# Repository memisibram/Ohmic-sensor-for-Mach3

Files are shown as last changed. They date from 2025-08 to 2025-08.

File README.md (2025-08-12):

# Ohmic-sensor-for-Mach3
Touch ohmic sensor for Mach3 plasma cutters

### About the project
This project is designed for use in plasma cutters using a Mach3 control card that communicates via a USB port.

While performing a probe search with the torch, the pilot arc cable is disabled and the torch nozzle is connected to an opamp integrated circuit. Once the probe search is complete, the pilot arc cable is reconnected, allowing the ohmic sensor to be used in HF-initiated pilot arc plasma cutters.

Project video.
 - Video: [https://youtu.be/aqT4PSTSzog](https://youtu.be/aqT4PSTSzog)

### Pictures
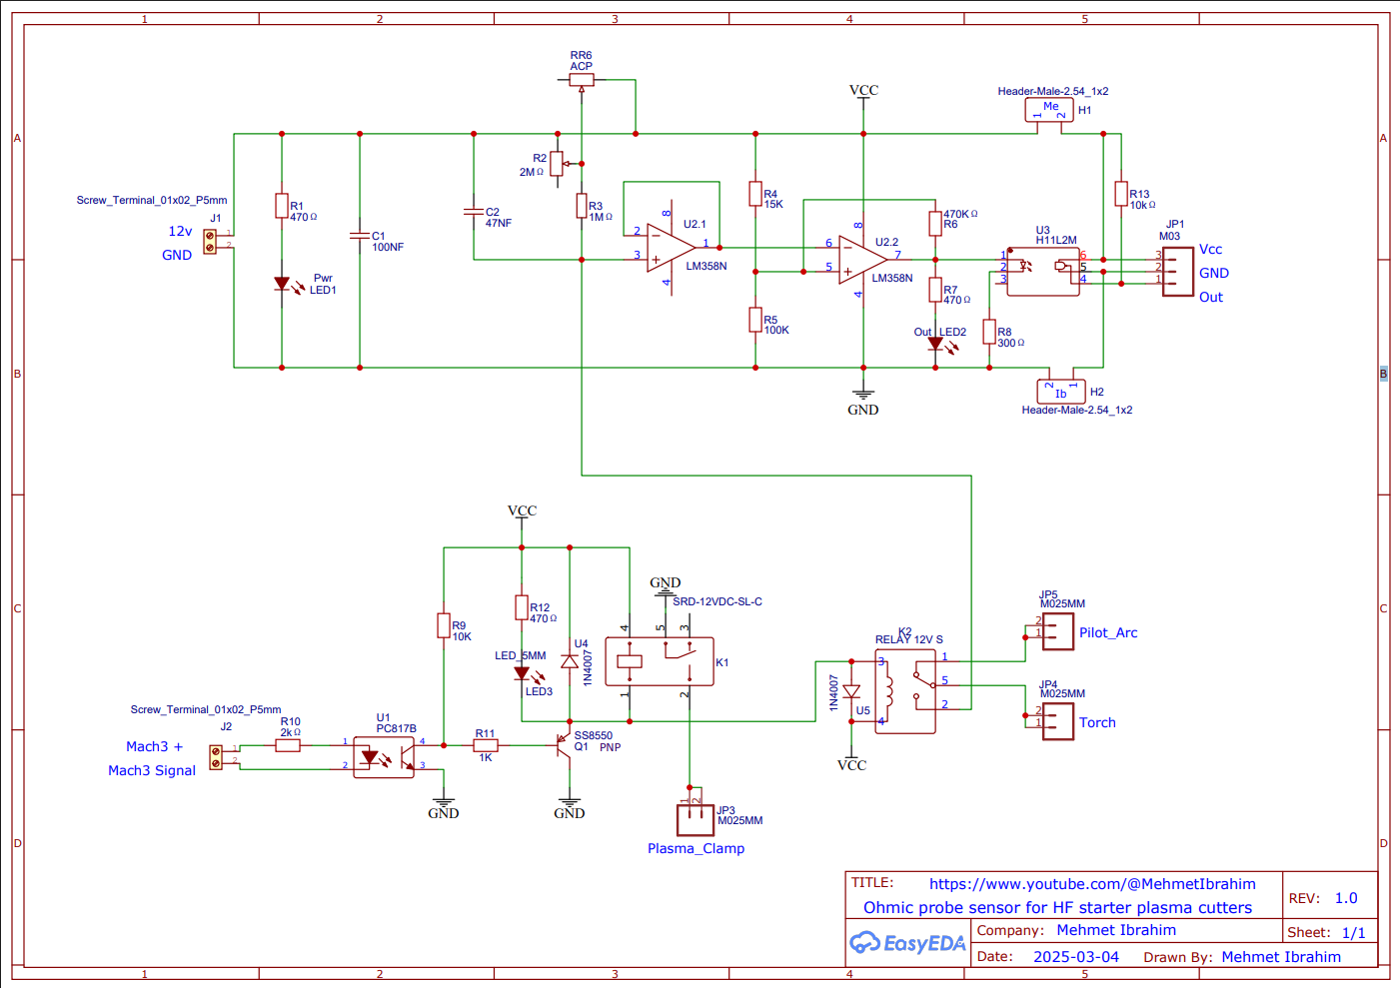
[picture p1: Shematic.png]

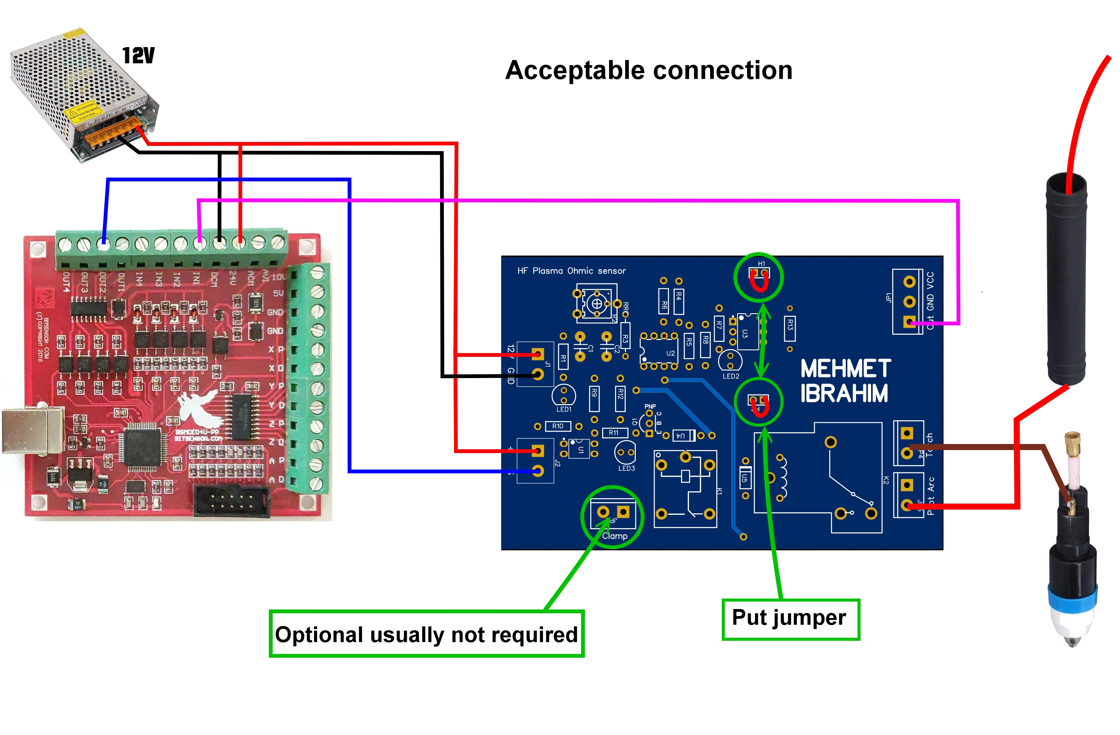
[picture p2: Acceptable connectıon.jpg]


### License GNU GPL v3.0

### Donation

  -  Paypal: memisibram@gmail.com or https://www.paypal.me/memisibram

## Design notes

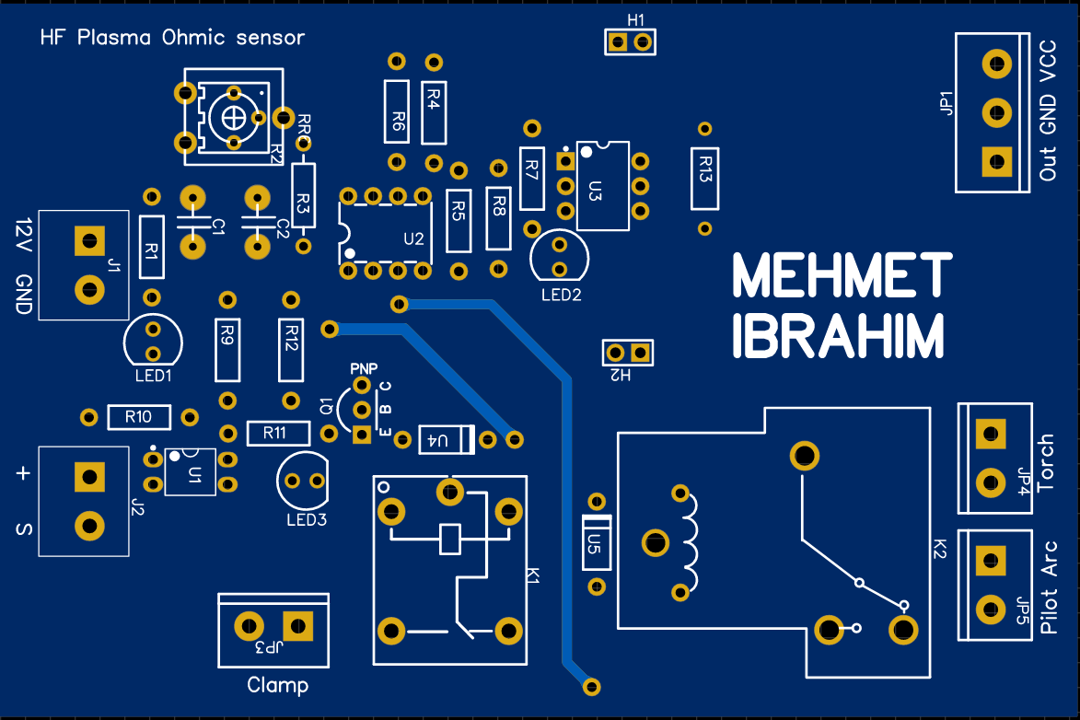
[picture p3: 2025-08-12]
Screenshot 2025-03-24 004826.png

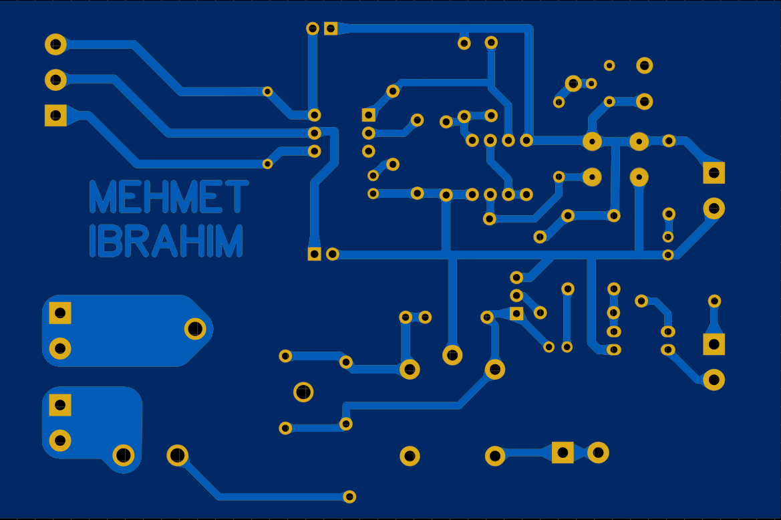
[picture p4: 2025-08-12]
Screenshot 2025-03-24 004859.png

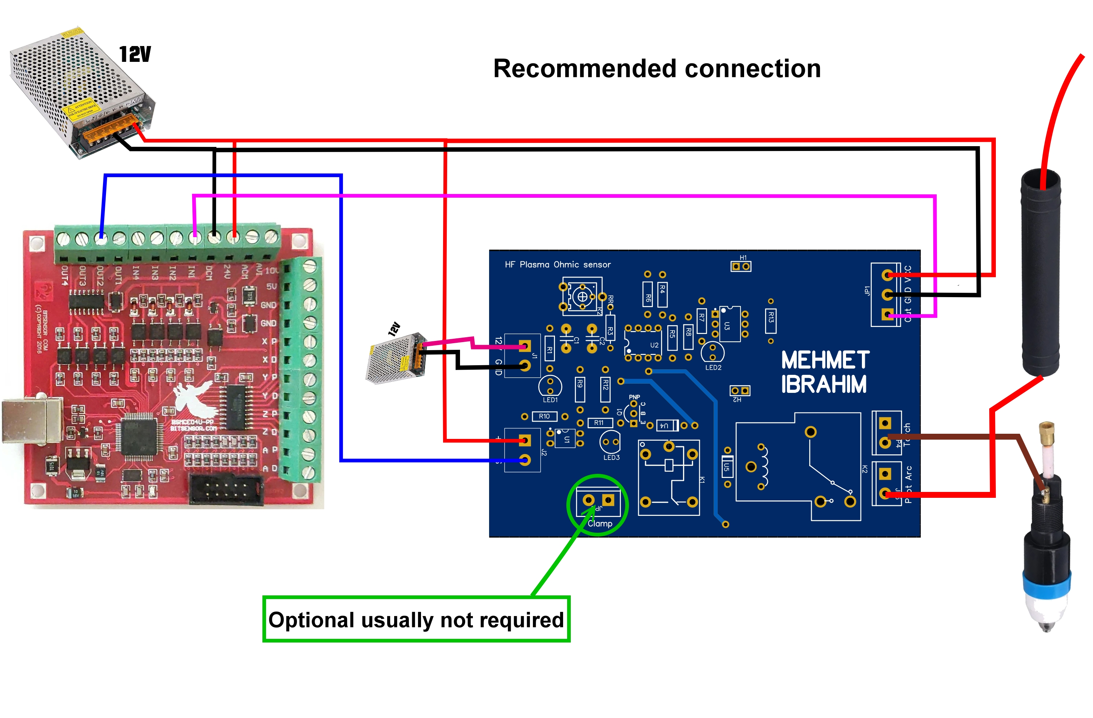
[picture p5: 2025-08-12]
Recommended connectıon.jpg

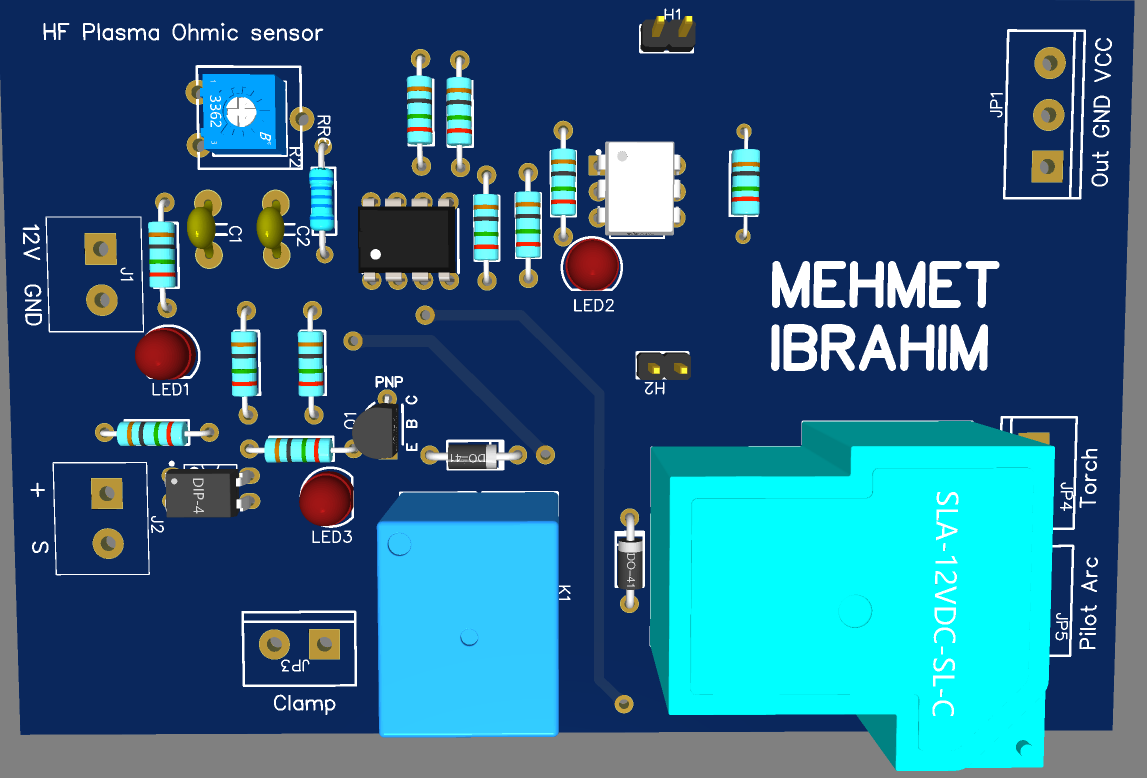
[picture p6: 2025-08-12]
Screenshot 2025-03-24 015735.png

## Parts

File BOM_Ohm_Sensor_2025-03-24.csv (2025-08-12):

ID | Name | Designator | Footprint | Quantity | Manufacturer Part | Manufacturer | Supplier | Supplier Part | Price
1 | ACP | RR6 | ACP SPAIN | 1
2 | 1MΩ | R3 | RES-TH_BD2.2-L6.5-P10.50-D0.6 | 1 | CFR0W4J0105A50 | UNI-ROYAL(厚声) | LCSC | C61306 | 0.008
3 | 2kΩ | R10 | RES-TH_BD2.4-L6.3-P10.30-D0.6 | 1 | MFR-25FRE52-2K | YAGEO(国巨) | LCSC | C1745563 | 0.011
4 | 10kΩ | R13 | RES-TH_BD2.7-L6.2-P10.20-D0.4 | 1 | CR1/4W-10K±5%-ST52 | VO(翔胜) | LCSC | C2894649 | 0.003
5 | SS8550 | Q1 | TO-92-3_L4.8-W3.7-P2.54-L | 1 | SS8550CTA | onsemi(安森美) | LCSC | C327518 | 0.107
6 | Screw_Terminal_01x02_P5mm | J2,J1 | TERMINALBLOCK_ONSHORE_1X02_P5.00MM_HORIZONTAL | 2
7 | Header-Male-2.54_1x2 | H2,H1 | HDR-TH_2P-P2.54-V-M-1 | 2 | 826629-2 | TE Connectivity(泰科电子) | LCSC | C86471 | 0.443
8 | LM358N | U2 | PDIP-8_L10.2-W5.9-P2.54-LS7.6-BL | 1 | LM358N/NOPB | TI(德州仪器) | LCSC | C83405 | 0.806
9 | 1N4007 | U5,U4 | DO-41_BD2.4-L4.7-P8.70-D0.6-RD | 2 | 1N4007 | CJ(江苏长电/长晶) | LCSC | C5261026 | 0.019
10 | H11L2M | U3 | DIP-6_L8.5-W6.4-P2.54-LS7.6-BL | 1 | H11L2M | onsemi(安森美) | LCSC | C258255 | 1.486
11 | PC817B | U1 | DIP-4_L4.6-W6.5-P2.54-LS7.6-BL | 1 | PC817B | 华润华晶 | LCSC | C115499 | 0.053
12 | 2MΩ | R2 | RES-ADJ-TH_3362P | 1 | 3362P-1-205LF | BOURNS | LCSC | C124582 | 0.342
13 | 470Ω | R12,R7,R1 | RES-TH_BD2.4-L6.3-P10.30-D0.6 | 3 | RN 1/4W 300R F T/B A1 | Tyohm(幸亚电阻) | LCSC | C410638 | 0.01
14 | 1K | R11 | RES-TH_BD2.4-L6.3-P10.30-D0.6 | 1 | RN 1/4W 300R F T/B A1 | Tyohm(幸亚电阻) | LCSC | C410638 | 0.01
15 | 10K | R9 | RES-TH_BD2.4-L6.3-P10.30-D0.6 | 1 | RN 1/4W 300R F T/B A1 | Tyohm(幸亚电阻) | LCSC | C410638 | 0.01
16 | 300Ω | R8 | RES-TH_BD2.4-L6.3-P10.30-D0.6 | 1 | RN 1/4W 300R F T/B A1 | Tyohm(幸亚电阻) | LCSC | C410638 | 0.01
17 | 470KΩ | R6 | RES-TH_BD2.4-L6.3-P10.30-D0.6 | 1 | RN 1/4W 300R F T/B A1 | Tyohm(幸亚电阻) | LCSC | C410638 | 0.01
18 | 100K | R5 | RES-TH_BD2.4-L6.3-P10.30-D0.6 | 1 | RN 1/4W 300R F T/B A1 | Tyohm(幸亚电阻) | LCSC | C410638 | 0.01
19 | 15K | R4 | RES-TH_BD2.4-L6.3-P10.30-D0.6 | 1 | RN 1/4W 300R F T/B A1 | Tyohm(幸亚电阻) | LCSC | C410638 | 0.01
20 | LED_5MM | LED3 | LED-TH_BD5.0-P2.54-FD_C9900023552 | 1 | LED_5MM | null | LCSC | C9900023552
21 | Out | LED2 | LED-TH_BD5.0-P2.54-FD_C9900023552 | 1 | LED_5MM | null | LCSC | C9900023552
22 | Pwr | LED1 | LED-TH_BD5.0-P2.54-FD_C9900023552 | 1 | LED_5MM | null | LCSC | C9900023552
23 | SRD-12VDC-SL-C | K1 | RELAY-TH_SRD-XXVDC-XL-C | 1 | SRD-12VDC-SL-C | 松乐 | LCSC | C30431 | 0.311
24 | 47NF | C2 | CERAMIC CAPACITOR 100NF | 1 | CT4-0805Y104M500 | LCSC | LCSC | undefined
25 | 100NF | C1 | CERAMIC CAPACITOR 100NF | 1 | CT4-0805Y104M500 | LCSC | LCSC | undefined
26 | M03 | JP1 | SCREWTERMINAL-5MM-3 | 1
27 | M025MM | JP5,JP4,JP3 | SCREWTERMINAL-5MM-2 | 3
28 | RELAY 12V S | K2 | RELAY-TH_SLA-12VDC-SL-C | 1 | SLA-12VDC-SL-C | SONGLE | LCSC | C125736 | 1.039

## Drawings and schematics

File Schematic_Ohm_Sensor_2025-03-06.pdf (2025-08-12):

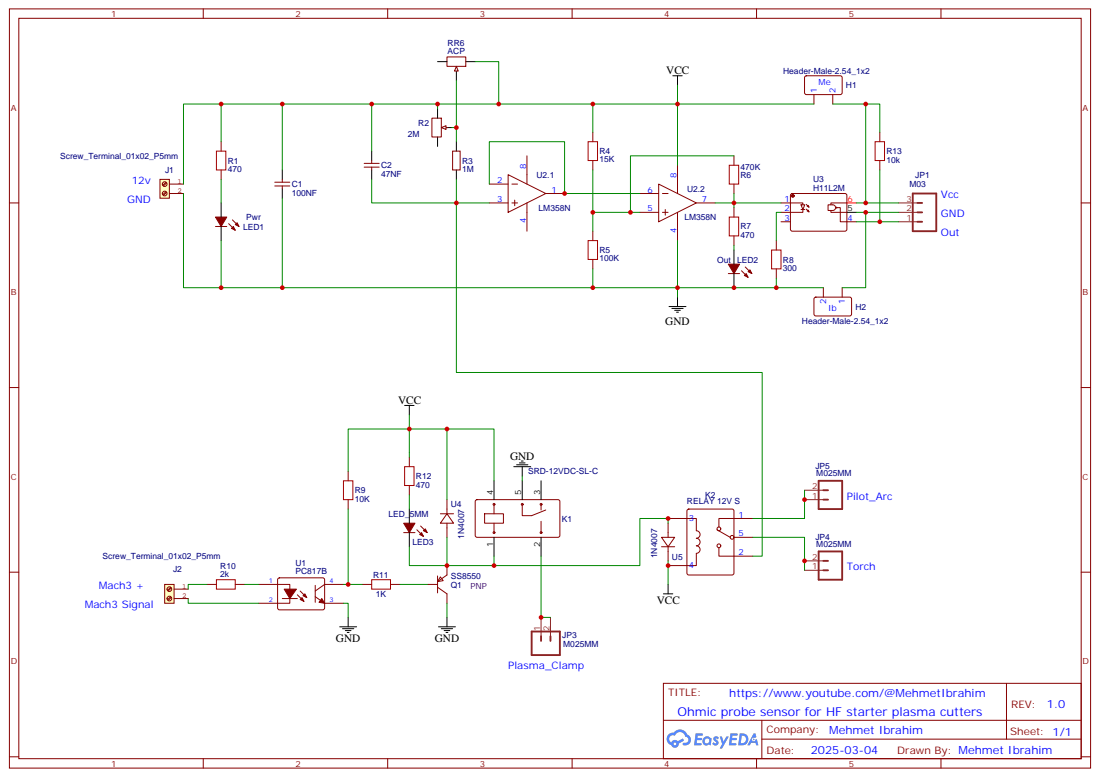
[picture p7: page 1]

TITLE:
Ohmic probe sensor for HF starter plasma cutters

https://www.youtube.com/@MehmetIbrahim

Drawn By: Mehmet Ibrahim

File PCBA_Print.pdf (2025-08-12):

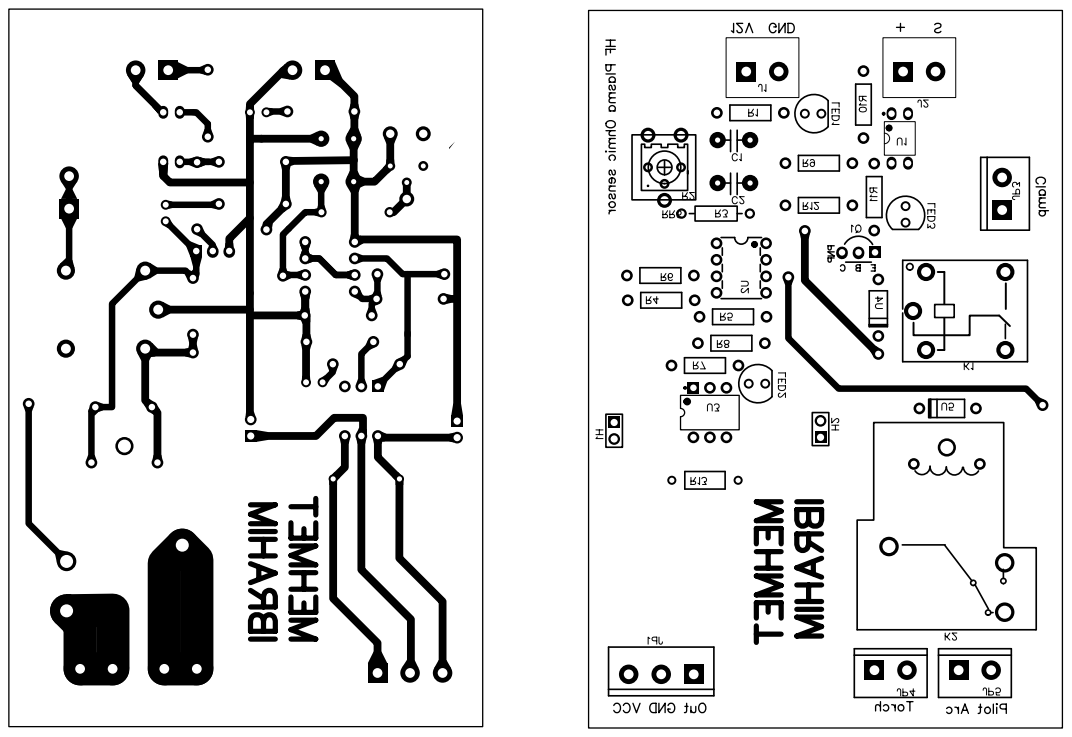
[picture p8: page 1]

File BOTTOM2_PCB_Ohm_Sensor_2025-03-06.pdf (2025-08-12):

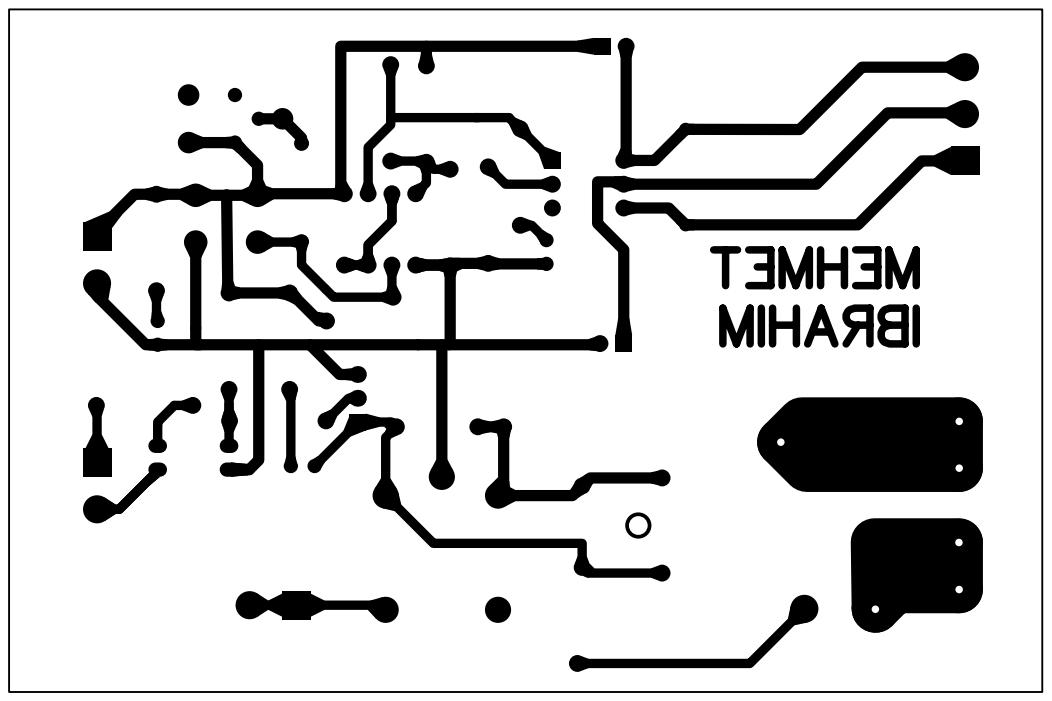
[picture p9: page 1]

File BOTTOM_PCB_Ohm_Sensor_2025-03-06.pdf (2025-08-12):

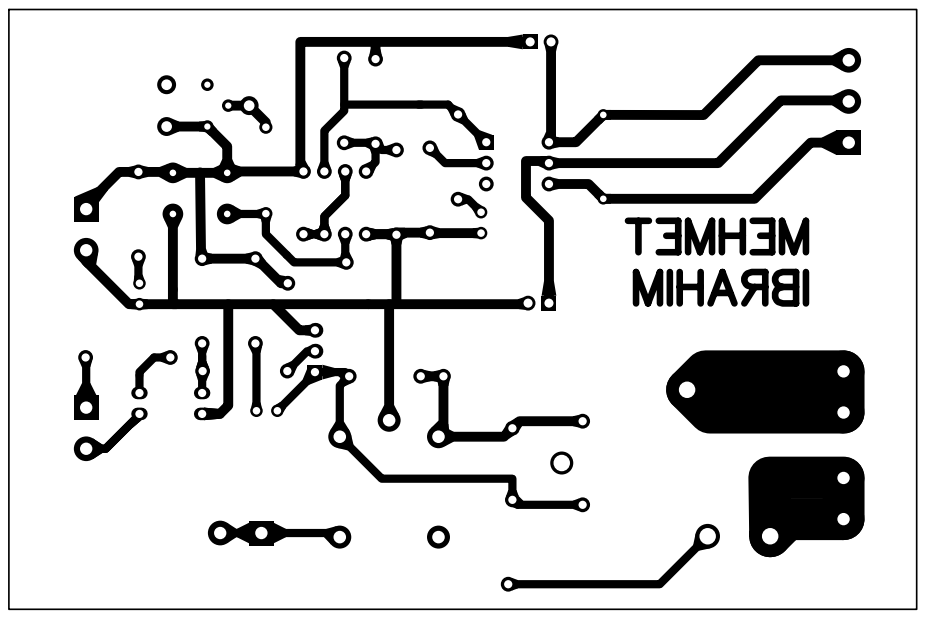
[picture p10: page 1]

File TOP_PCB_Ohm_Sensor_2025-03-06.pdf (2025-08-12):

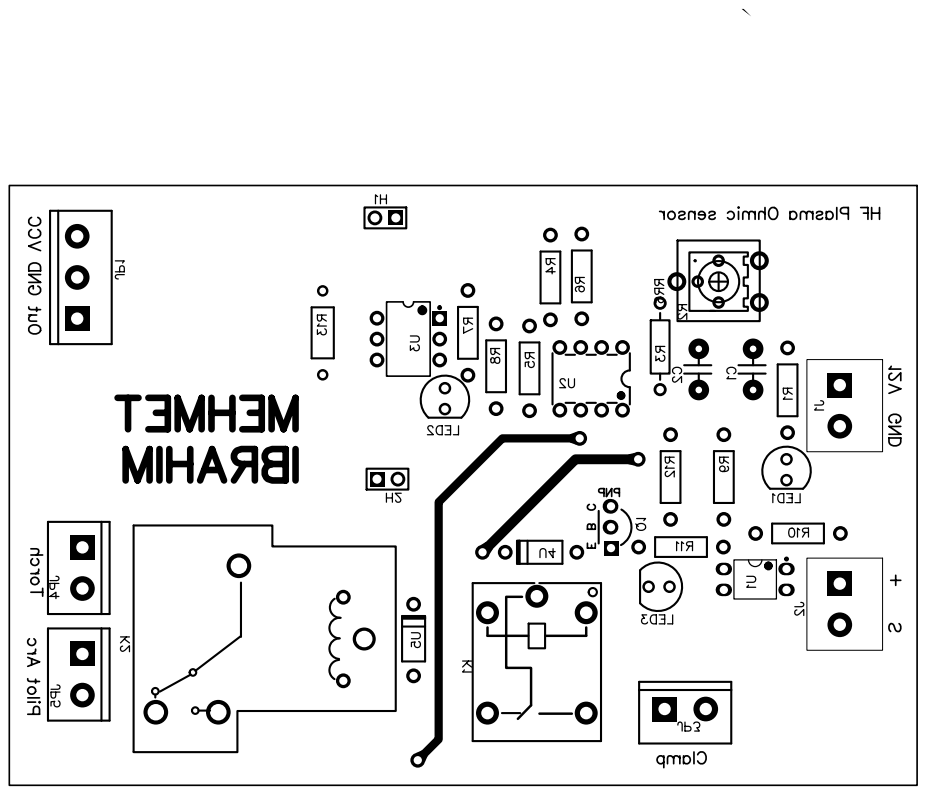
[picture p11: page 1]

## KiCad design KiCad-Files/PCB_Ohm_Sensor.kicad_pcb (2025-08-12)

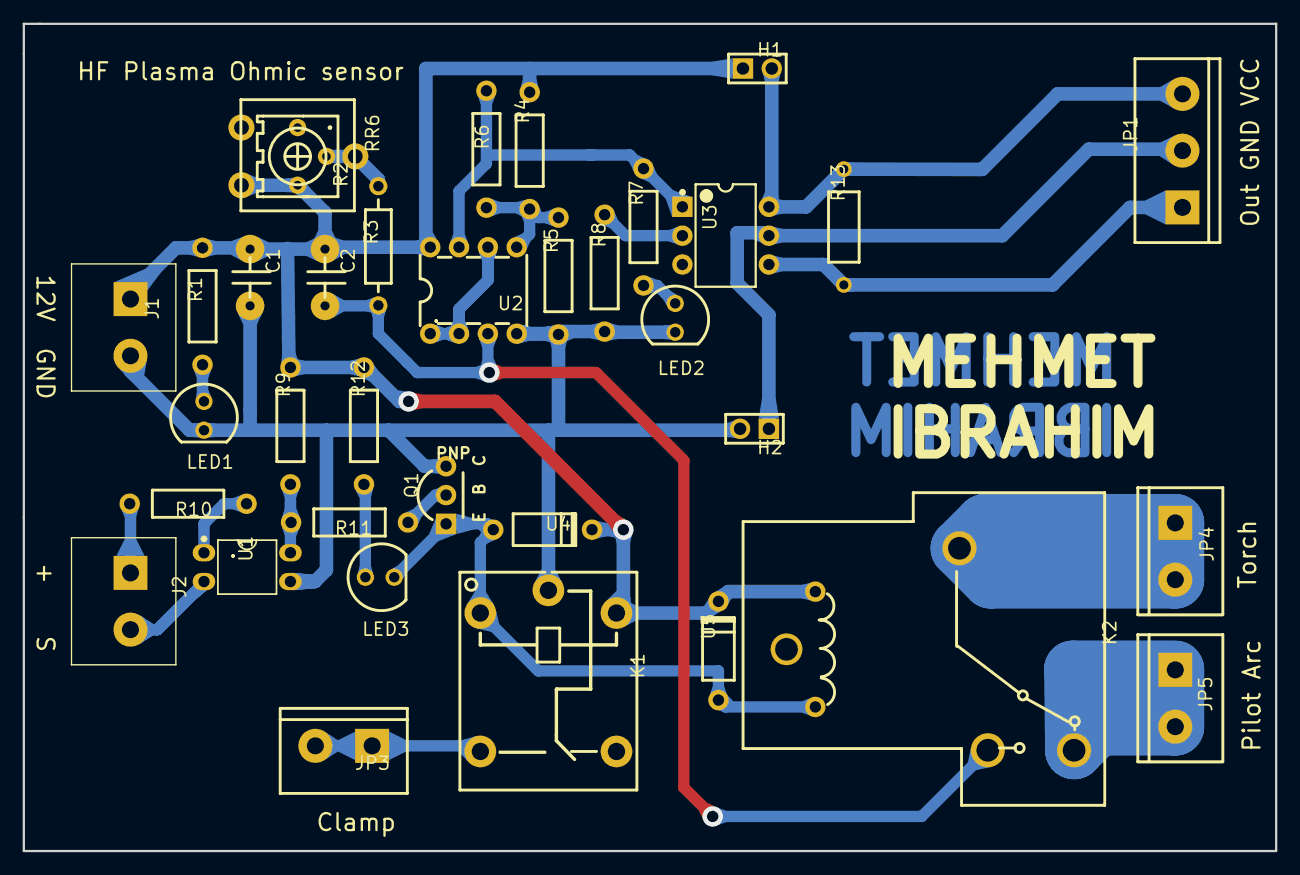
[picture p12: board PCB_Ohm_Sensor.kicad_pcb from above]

Board: 2 copper layers, 110.4 x 72.9 mm, 35 parts (0 on the bottom side), 23 nets.

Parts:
C1: 100NF; CERAMIC CAPACITOR 100NF
C2: 47NF; CERAMIC CAPACITOR 100NF
H1, H2: Header-Male-2.54_1x2; HDR-TH_2P-P2.54-V-M-1
J1, J2: REF; TERMINALBLOCK_ONSHORE_1X02_P5.00MM_HORIZONTAL
JP1: M03; SCREWTERMINAL-5MM-3
JP3, JP4, JP5: M025MM; SCREWTERMINAL-5MM-2
K1: SRD-12VDC-SL-C; RELAY-TH_SRD-XXVDC-XL-C
K2: RELAY 12V S; RELAY-TH_SLA-12VDC-SL-C
LED1: Pwr; LED-TH_BD5.0-P2.54-FD_C9900023552
LED2: Out; LED-TH_BD5.0-P2.54-FD_C9900023552
LED3: LED_5MM; LED-TH_BD5.0-P2.54-FD_C9900023552
Q1: SS8550; TO-92-3_L4.8-W3.7-P2.54-L
R1, R7, R12: 470Ω; RES-TH_BD2.4-L6.3-P10.30-D0.6
R2: 2MΩ; RES-ADJ-TH_3362P
R3: 1MΩ; RES-TH_BD2.2-L6.5-P10.50-D0.6
R4: 15K; RES-TH_BD2.4-L6.3-P10.30-D0.6
R5: 100K; RES-TH_BD2.4-L6.3-P10.30-D0.6
R6: 470KΩ; RES-TH_BD2.4-L6.3-P10.30-D0.6
R8: 300Ω; RES-TH_BD2.4-L6.3-P10.30-D0.6
R9: 10K; RES-TH_BD2.4-L6.3-P10.30-D0.6
R10: 2kΩ; RES-TH_BD2.4-L6.3-P10.30-D0.6
R11: 1K; RES-TH_BD2.4-L6.3-P10.30-D0.6
R13: 10kΩ; RES-TH_BD2.7-L6.2-P10.20-D0.4
RR6: ACP; ACP SPAIN
U1: PC817B; DIP-4_L4.6-W6.5-P2.54-LS7.6-BL
U2: LM358N; PDIP-8_L10.2-W5.9-P2.54-LS7.6-BL
U3: H11L2M; DIP-6_L8.5-W6.4-P2.54-LS7.6-BL
U4, U5: 1N4007; DO-41_BD2.4-L4.7-P8.70-D0.6-RD

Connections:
GND: C1.2, H2.2, J1.2, K1.5, LED1.2, LED2.2, Q1.3, R5.2, R8.2, U1.3, U2.4
J2_1: J2.1, R10.1
JP4_1: JP4.1, JP4.2, K2.5
JP5_1: JP5.1, JP5.2, K2.1
K1_2: JP3.1, JP3.2, K1.2
LED3_2: K1.1, K2.3, LED3.2, Q1.1, U4.2, U5.2
R1_2: LED1.1, R1.2
R2_2: R2.2, R3.1, RR6.3
R7_2: LED2.1, R7.2
R8_1: R8.1, U3.2
R11_2: Q1.2, R11.2
R12_2: LED3.1, R12.2
U1_1: R10.2, U1.1
U1_2: J2.2, U1.2
U1_4: R9.2, R11.1, U1.4
U2_3: C2.2, K2.2, R3.2, U2.3
U2_5: R4.2, R5.1, R6.2, U2.5
U2_6: U2.1, U2.2, U2.6
U2_7: R6.1, R7.1, U2.7, U3.1
U3_4: JP1.1, R13.2, U3.4
U3_5: H2.1, JP1.2, U3.5
U3_6: H1.2, JP1.3, R13.1, U3.6
VCC: C1.1, C2.1, H1.1, J1.1, K1.4, K2.4, R1.1, R2.3, R4.1, R9.1, R12.1, RR6.2, U2.8, U4.1, U5.1
